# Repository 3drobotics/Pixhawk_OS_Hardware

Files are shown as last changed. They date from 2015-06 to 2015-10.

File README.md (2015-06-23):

# Pixhawk_OS_Hardware
Design files for the open hardware designs used by 3DR

Some of the files in this Repository are derivitives of the PX4 project.

PX4 is an open hardware design, following the OSHW 1.1 definition licensed under the Creative Commons Attribution-ShareAlike 3.0 Unported (CC BY-SA 3.0) license.  Website at: http://pixhawk.ethz.ch/px4/

That includes 
FMUv3
IMUv3
PSMv3

the following licence applies to these files.

UNLESS OTHERWISE MUTUALLY AGREED TO BY THE PARTIES IN WRITING, LICENSOR OFFERS THE WORK AS-IS AND MAKES NO REPRESENTATIONS OR WARRANTIES OF ANY KIND CONCERNING THE WORK, EXPRESS, IMPLIED, STATUTORY OR OTHERWISE, INCLUDING, WITHOUT LIMITATION, WARRANTIES OF TITLE, MERCHANTIBILITY, FITNESS FOR A PARTICULAR PURPOSE, NONINFRINGEMENT, OR THE ABSENCE OF LATENT OR OTHER DEFECTS, ACCURACY, OR THE PRESENCE OF ABSENCE OF ERRORS, WHETHER OR NOT DISCOVERABLE. SOME JURISDICTIONS DO NOT ALLOW THE EXCLUSION OF IMPLIED WARRANTIES, SO SUCH EXCLUSION MAY NOT APPLY TO YOU. EXCEPT TO THE EXTENT REQUIRED BY APPLICABLE LAW, IN NO EVENT WILL LICENSOR BE LIABLE TO YOU ON ANY LEGAL THEORY FOR ANY SPECIAL, INCIDENTAL, CONSEQUENTIAL, PUNITIVE OR EXEMPLARY DAMAGES ARISING OUT OF THIS LICENSE OR THE USE OF THE WORK, EVEN IF LICENSOR HAS BEEN ADVISED OF THE POSSIBILITY OF SUCH DAMAGES. http://creativecommons.org/licenses/by-sa/3.0/

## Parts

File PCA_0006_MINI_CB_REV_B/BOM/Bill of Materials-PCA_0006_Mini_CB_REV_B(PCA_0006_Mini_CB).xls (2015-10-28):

Manufacturer 1 | Manufacturer Part Number 1 | Supplier Part Number 1 | 3DR_PARTNO | Description | Designator | Value | Quantity | Footprint | Mfg Part Num (Alternate) | Mfg Name (Alternate) | Supplier Unit Price 1 | Total Cost per
Molex, LLC | 5023861570 | WM4958DKR-ND | ECM0530 | Connector, Receptacle, 15Pos, 1.25MM, R/A, SMD, Tin | 1 |  | 1 | CLICKMATE_H15 |  |  | $1.67 | $1.67
Molex, LLC | 5023860470 | WM4948CT-ND | ECM0531 | Connector, Receptacle, 4Pos, 1.25MM, R/A, SMD, Tin | 2, 3 |  | 2 | CLICKMATE_H4 |  |  | $0.78 | $1.55
Molex, LLC | 5023860670 | WM3917CT-ND | ECM0532 | 1.25 W/B SGL R/A REC ASSY 6CKT | 5, 11 |  | 2 | CLICKMATE_H6 |  |  | $0.92 | $1.84
Molex, LLC | 5023860870 | WM4951CT-ND | ECM0533 | Connector, Receptacle, 8Pos, 1.25MM, R/A, SMD, Tin | 7 |  | 1 | CLICKMATE_H8 |  |  | $1.02 | $1.02
Molex, LLC | 5024940670 | WM2283CT-ND | ECM0534 | Connector, Receptacle, 6Pos, 2.00MM, R/A, PCB, Tin | 9 |  | 1 | CLICKMATE_H6_2MM |  |  | $1.04 | $1.04
TE Connectivity / Raychem | PESD0402-140 | 650-PESD0402-140 | ECM0837 | Diode, TVS, 14VWM, 40VC, 0402, SMD | D2, D3, D101, D103, D702 |  | 5 | 0402-TVS |  |  | $0.09 | $0.45
VISHAY SEMICONDUCTOR | MSS1P4-M3/89A | 2335156 | ECM0900 | Diode, Schottky, 40V, 1A, MicroSMP, SMD | D701 |  | 1 | MICROSMP |  |  | $0.12 | $0.12
AVX Corp/Kyocera Corp | KNH16C104DA5TS | 478-6878-1-ND | ECM0719 | Capacitor, Filter, 0.1uF, 25V, 2A, 0603, SMD | L1, L3, L101, L103, L701 |  | 5 | KYOCERA-KNH16-DA |  |  | $0.09 | $0.47
 |  |  | PCB0007 | PCB, Carrier Mini, PX2, Board | PCB0007 | PCB0007 | 1 |  |  |  |  | $0.00
3DR | PCA-0007 | PCA-0007 | PCA0007 | PCA, PSM, PX4, Assembly | PSM ? |  | 1 | PSM |  |  | $17.00 | $17.00
Hirose Electric Co Ltd | DF17(1.0H)-80DP-0.5V(57) | DF17(1.0H)-80DP-0.5V(57)-ND | ECM0528 | Connector, Header, 80Pos, .5MM, DUAL, SMD, Au | U$1 |  | 1 | CON-DF17-80M |  |  | $1.50 | $1.50
 |  |  |  |  |  |  |  |  |  |  |  | $0.00
 |  |  |  |  |  |  |  |  |  |  |  | $0.00
 |  |  |  |  |  |  |  |  |  |  |  | $0.00
 |  |  |  |  |  |  |  |  |  |  |  | $0.00
 |  |  |  |  |  |  |  |  |  |  |  | $0.00
 |  |  |  |  |  |  |  |  |  |  |  | $0.00
 |  |  |  |  |  |  |  |  |  |  |  | $0.00
 |  |  |  |  |  |  |  |  |  |  |  | $0.00
 |  |  |  |  |  |  |  |  |  |  |  | $0.00
 |  |  |  |  |  |  |  |  |  |  |  | $0.00
 |  |  |  |  |  |  |  |  |  |  |  | $0.00
 |  |  |  |  |  |  |  |  |  |  |  | $0.00
 |  |  |  |  |  |  |  |  |  |  |  | $0.00
 |  |  |  |  |  |  |  |  |  |  |  | $0.00
 |  |  |  |  |  |  |  |  |  |  |  | $0.00
 |  |  |  |  |  |  |  |  |  |  |  | $0.00
 |  |  |  |  |  |  |  |  |  |  |  | $0.00
 |  |  |  |  |  |  |  |  |  |  |  | $0.00
 |  |  |  |  |  |  |  |  |  |  |  | $0.00
 |  |  |  |  |  |  |  |  |  |  |  | $0.00
 |  |  |  |  |  |  |  |  |  |  |  | $0.00
 |  |  |  |  |  |  |  |  |  |  |  | $0.00
 |  |  |  |  |  |  |  |  |  |  |  | $0.00
 |  |  |  |  |  |  |  |  |  |  |  | $0.00
 |  |  |  |  |  |  |  |  |  |  |  | $0.00
 |  |  |  |  |  |  |  |  |  |  |  | $0.00
 |  |  |  |  |  |  |  |  |  |  |  | $0.00
 |  |  |  |  |  |  |  |  |  |  |  | $0.00
 |  |  |  |  |  |  |  |  |  |  |  | $0.00
 |  |  |  |  |  |  |  |  |  |  |  | $0.00
 |  |  |  |  |  |  |  |  |  |  |  | $0.00
 |  |  |  |  |  | Total Qty. | 21 |  |  |  | Total Cost | $26.67

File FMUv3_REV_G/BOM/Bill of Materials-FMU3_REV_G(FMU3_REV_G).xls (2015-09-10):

Manufacturer 1 | Manufacturer Part Number 1 | Supplier Part Number 1 | 3DR_PARTNO | Description | Designator | Value | Quantity | Footprint | Mfg Part Num (Alternate) | Mfg Name (Alternate) | Supplier Unit Price 1 | Total Cost per
Yageo | CC0402ZRY5V7BB104 | 311-1047-1-ND | ECM0700 | CAP CER 0.1UF 16V Y5V 0402 | C1001, C3001, C3002, C3003, C3004, C4003, C4005, C4006, C5001, C5005, C5007, C5009, C5010, C5011, C5012, C5014, C5015, C7001, C7002, C7003, C7006, C8001, C8002, C8003, C10002 | 0u1 | 25 | 0402-CAP |  |  | $0.00242 | $0.06
TDK Corporation | C1005C0G1H080C050BA | 445-4890-1-ND | ECM0710 | CAP CER 8PF 50V C0G 0402 | C1002, C1003, C7004, C7005 | 8p | 4 | 0402-CAP |  |  | $0.01 | $0.02
TDK Corporation | C1608X6S1C225K080AC | 445-7438-1-ND | ECM0619 | CAP CER 2.2UF 16V 10% X6S 0603 | C4001, C4002, C5013, C5016 | 2u2 | 4 | 0603-CAP |  |  | $0.06 | $0.22
TDK Corporation | C1005X6S1E224K050BC | 445-7362-1-ND | ECM | CAP CER 0.22UF 25V 10% X7R 0402 | C4007 | 0u22 | 1 | 0402-CAP |  |  | $0.02 | $0.02
Samsung Electro-Mechanics America, Inc. | CL21B475KOFNNNE | 1276-2873-1-ND | ECM0622 | CAP CER 4.7UF 16V 10% X7R 0805 | C4008 | 4u7 | 1 | 0805 |  |  | $0.06 | $0.06
Samsung Electro-Mechanics America, Inc. | CL21A106KAYNNNE | 1276-2891-1-ND | ECM0714 | CAP CER 10UF 25V 10% X5R 0805 | C5002, C10001 | 10u/25 | 2 | 0805-CAP |  |  | $0.06 | $0.11
Yageo | CC0402KRX7R7BB103 | 311-1042-1-ND | ECM0711 | CAP CER 10000PF 16V 10% X7R 0402 | C5003, C10003 | 10n | 2 | 0402-CAP |  |  | $0.00249 | $0.00498
Yageo | CC0603ZRY5V7BB105 | 311-1372-1-ND | ECM0705 | CAP CER 1UF 16V Y5V 0603 | C5004, C10005 | 1u | 2 | 0603-CAP |  |  | $0.01 | $0.02
Samsung Electro-Mechanics America, Inc. | CL21A226MAQNNNE | 1276-2908-1-ND | ECM0715 | CAP CER 22UF 25V 20% X5R 0805 | C5006, C5008 | 22u/25V | 2 | 0805-CAP |  |  | $0.39 | $0.78
Murata Electronics North America | GRM21BR60G107ME15L | 490-10510-1-ND |  |  | C5100, C5101 | 100uF | 2 | C0805 |  |  | $0.43 | $0.86
TDK Corporation | C1608X5R1A106K080AC | 445-7486-1-ND | ECM0712 | CAP CER 10UF 10V 10% X5R 0603 | C10004 | 10u | 1 | 0603-CAP |  |  | $0.13 | $0.13
ON Semiconductor | RB751V40T1G | RB751V40T1GOSCT-ND | ECM0839 | DIODE SCHOTTKY 30V 0.03A SOD323 | D5001 | 30V | 1 | SOD323 |  |  | $0.05 | $0.05
TE Connectivity / Raychem | PESD0402-140 | 650-PESD0402-140 | ECM0837 | TVS DIODE 14VWM 40VC 0402 | D8001, D8002 | 40v | 2 | 0402-TVS |  |  | $0.09 | $0.19
NXP Semiconductors | PMEG2005CT,215 | 568-6500-1-ND | ECM0838 | DIODE SCHOTTKY 20V 500MA TO236AB | D10001 | 20V | 1 | SOT23-3 |  |  | $0.10 | $0.10
Bel Fuse Inc. | 0ZCA0035FF2G | 507-1479-1-ND | ECM0802 | PTC RESTTBLE 0.35A 16V CHIP 1206 | F10001 | 0.35A | 1 | PTC-1206 |  |  | $0.11 | $0.11
Molex Inc. | 0473460001 | WM17141DKR-ND | ECM0486 | MICRO USB B, BOTTOM MOUNT | J2001 |  | 1 | MOLEX-47346-0001 |  |  | $0.52 | $0.52
 |  |  |  |  | JP1 |  | 1 | SJ_3_NO_PLACE_1-2_short |  |  |  | $0.00
AVX Corp/Kyocera Corp | KNH16C104DA5TS | 478-6878-1-ND | ECM0719 | FILTER CAP 0.1UF 2A 25V 0603 | L2001, L2002, L5001 | 0u1 | 3 | KYOCERA-KNH16-DA |  |  | $0.09 | $0.26
Kingbright | APTD1608CGCK | 754-1545-2-ND | ECM0494 | LED GREEN ROUND CLEAR SMD | LED1, LED2, LED6001, LED6002, LED6003, LED6004, LED6005, LED6006, LED6007, LED6008, LED6009 | GREEN | 11 | 0603-LED-Blue |  |  | $0.07 | $0.78
Kingbright | APTD1608SECK/J4-PF | 754-1802-1-ND | ECM0515 | LED 1.6X0.8 DOME ORN CLEAR SMD | LED6010, LED6011 | AMBER | 2 | 0603-LED |  |  | $0.18 | $0.37
 |  |  | PCB005 | PCB,FMU, PX2, Board | PCB005 | PCB005 | 1 |  |  |  |  | $0.00
Infineon Technologies | MMBT 3906 LT1 | MMBT3906LT1INCT-ND | ECM0833 | TRANSISTOR SWITCHING PNP SOT-23 | Q5001 |  | 1 | SOT23-BEC |  |  | $0.03 | $0.03
Diodes Incorporated | BSS123-7-F | BSS123-FDICT-ND | ECM0547 | MOSFET N-CH 100V 170MA SOT23-3 | Q6001 | 100V | 1 | SOT23 |  |  | $0.06 | $0.06
Yageo | RC0402FR-07220RL | 311-220LRCT-ND | ECM0821 | RES 220 OHM 1/16W 1% 0402 SMD | R1, R2, R1022, R4001, R4002, R6003, R6004, R6005, R6006, R6007, R6008, R6009, R6010, R6011, R6012, R6013, R6014, R6015, R7003, R7004, R7010, R7011, R7012 | 220R | 23 | 0402-RES |  |  | $0.00176 | $0.04
Yageo | RC0402FR-07470RL | 311-470LRCT-ND | ECM0823 | RES 470 OHM 1/16W 1% 0402 SMD | R1001 | 470R | 1 | 0402-RES |  |  | $0.00176 | $0.00176
Yageo | RC0402FR-0710KL | 311-10.0KLRCT-ND | ECM0800 | RES 10K OHM 1/16W 1% 0402 SMD | R1002, R5001, R5006, R6002, R7001, R7002, R8001 | 10K | 7 | 0402-RES |  |  | $0.00176 | $0.01
Panasonic Electronic Components | ERA-2AEB103X | P10KDCCT-ND | ECM0810 | RES 10K OHM 1/16W .1% 0402 SMD | R2001, R2002 | 10K | 2 | 0402-RES |  |  | $0.07 | $0.15
Yageo | RC0402FR-071ML | 311-1.00MLRCT-ND | ECM0806 | RES 1M OHM 1/16W 1% 0402 SMD | R2003, R2004 | 1M | 2 | 0402-RES |  |  | $0.00176 | $0.00352
Yageo | RC0402FR-071K5L | 311-1.50KLRCT-ND | ECM0803 | RES 1.5K OHM 1/16W 1% 0402 SMD | R3001, R3002, R3003, R3004, R6017 | 1K5 | 5 | 0402-RES |  |  | $0.00176 | $0.01
Yageo | RC0402FR-07120RL | 311-120LRCT-ND | ECM0820 | RES 120 OHM 1/16W 1% 0402 SMD | R3005, R3006, R3007, R3008, R3009, R3010 | 120R | 6 | 0402-RES |  |  | $0.00176 | $0.01
Samsung Electro-Mechanics America, Inc. | RC1005F182CS | 1276-4039-1-ND | ECM0807 | RES 1.8K OHM 1/16W 1% 0402 | R5002 | 1K8 | 1 | 0402-RES |  |  | $0.002 | $0.002
Samsung Electro-Mechanics America, Inc. | RC1608J100CS | 1276-5014-1-ND | ECM0811 | RES 10 OHM 1/10W 5% 0603 | R5003 | 10R | 1 | 0603-RES |  |  | $0.00164 | $0.00164
Samsung Electro-Mechanics America, Inc. | RC1005F102CS | 1276-3430-1-ND | ECM0804 | RES 1K OHM 1/16W 1% 0402 | R5005, R6001 | 1K | 2 | 0402-RES |  |  | $0.002 | $0.004
Panasonic | ERJ-2GEJ680X | 667-ERJ-2GEJ680X | ECM0816 | Thick Film Resistors - SMD 0402 68ohms 5% Tol | R6016 | 68R | 1 | 0402-RES |  |  | $0.00208 | $0.00208
Yageo | RC0402FR-07100KL | 311-100KLRCT-ND | ECM0818 | RES 100K OHM 1/16W 1% 0402 SMD | R10001 | 100K | 1 | 0402-RES |  |  | $0.00176 | $0.00176
Panasonic Electronic Components | EXB-2HV104JV | Y1104CT-ND | ECM0101 | RES ARRAY 100K OHM 8 RES 1506 | RN2001 | 100K | 1 | EXB2HV |  |  | $0.06 | $0.06
Panasonic Electronic Components | EXB-2HV103JV | Y1103CT-ND | ECM0546 | RES ARRAY 10K OHM 8 RES 1506 | RN2002 | 10K | 1 | EXB2HV |  |  | $0.06 | $0.06
Panasonic Electronic Components | EXB-2HV121JV | Y1121CT-ND | EMC, EMC, ECM0266, ECM0266 | RES ARRAY 120 OHM 8 RES 1506 | RN3001, RN3002, RN8001, RN8002 | 120R | 4 | EXB2HV |  |  | $0.06 | $0.26
InvenSense | MPU-9250 | 1428-1019-2-ND |  |  | U405 |  | 1 | MPU-9250 |  |  | $5.11 | $5.11
STMicroelectronics | STM32F427VIT6 |  |  | REV 3 Silicon or later IC MCU ARM 2MB FLASH 100LQFP | U1001 |  | 1 | TQFP100 |  |  | $9.75 | $9.75
Cypress Semiconductor Corp | FM25V02A-G | 428-3386-ND |  | IC FRAM 256KBIT 40MHZ 8SOIC | U1002 | 256Kb | 1 | SO08 |  |  | $3.31 | $3.31
ON Semiconductor | NUF2042XV6T1G | NUF2042XV6T1GOSDKR-ND | ECM0836 | IC FILTER USB ESD PROTECT SOT363 | U2001 |  | 1 | SOT563-6 |  |  | $0.15 | $0.15
3M | 2908-05WB-MG | 3M5607CT-ND | ECM0485 | CONN MICRO SD CARD PUSH-PUSH R/A | U2002 |  | 1 | MICROSD |  |  | $1.98 | $1.98
Texas Instruments | TXS0108ERGYR | 296-24806-1-ND | ECM0845 | IC XLATR VOLT-LVL 8B BDIR 20QFN | U3001, U3002, U8001 |  | 3 | QFN20-RGY |  |  | $0.85 | $2.56
Maxim Integrated | MAX3051EKA+T | MAX3051EKA+TCT-ND | ECM0831 | IC TXRX CAN 1MBPS SOT23-8 | U3003, U3004 | CAN | 2 | SOT23-8 |  |  | $1.93 | $3.86
Honeywell Microelectronics & Precision Sensors | HMC5983-TR | 342-1092-1-ND | ECM0672 | IC COMPASS 3 AXIS 16-LCC | U4002 |  | 1 | HMC5983-new |  |  | $1.50 | $1.50
Measurement Specialties | MS561101BA03-50 | 824-MS561101BA03-50 | ECM0835 | Board Mount Pressure Sensors | U4003 | 10-1200mbar | 1 | MS5611-01BA |  |  | $6.67 | $6.67
Micrel Inc. | MIC5332-SSYMT TR | 576-4110-1-ND | ECM0832 | IC REG LDO 3.3V 0.3A 8TMLF | U5001, U10002 | 3.3V | 2 | MLF-8-EPAD |  |  | $0.80 | $1.61
STMicroelectronics | STM32F100C8T6B | 497-10499-ND | EMC0842 | MCU 32BIT ARM 64K FLASH 48LQFP | U7001 |  | 1 | TQFP48 |  |  | $1.59 | $1.59
Texas Instruments | SN74LVC8T245RHLR | 296-18595-2-ND |  |  | U8002 |  | 1 | QFN20-RGY |  |  | $0.49 | $0.49
NXP Semiconductors | 74LVC2G240DP,125 | 568-8979-1-ND | ECM0817 | IC INVERTER DUAL 4-INPUT 8TSSOP | U8003 | INV | 1 | TSSOP8_SOT505-2 |  |  | $0.14 | $0.14
Texas Instruments | BQ24313DSGT | 296-23933-1-ND | ECM0824 | IC LI+ CHARGER FRONT END 8-SON | U10001 |  | 1 | QFN8-DSG |  |  | $0.87 | $0.87
Hirose Electric Co Ltd | DF40C(2.0)-20DS-0.4V(51) | H11905CT-ND | ECM0517 | CONN RCPT 20POS 0.4MM SMD GOLD | U$2 |  | 1 | DF-40C-20DS |  |  | $0.42 | $0.42
Hirose Electric Co Ltd | DF17(3.0H)-80DS-0.5V(57) | DF17(3.0H)-80DS-0.5V(57)-ND | ECM0518 | CONN RECEPT 80POS .5MM SMD W/FIT | U$9001 |  | 1 | CON-DF17-80F |  |  | $1.34 | $1.34
NDK | NX3225SA-24.000MHZ-STD-CSR-1 | 644-1052-1-ND | ECM0708 | CRYSTAL 24MHZ 8PF SMD | X1001, X7001 | 24MHz | 2 | OSCILLATOR-3.2X2.5 |  |  | $0.39 | $0.79
 |  |  |  |  |  |  |  |  |  |  |  | $0.00
 |  |  |  |  |  |  |  |  |  |  |  | $0.00
 |  |  |  |  |  |  |  |  |  |  |  | $0.00
 |  |  |  |  |  |  |  |  |  |  |  | $0.00
 |  |  |  |  |  |  |  |  |  |  |  | $0.00
 |  |  |  |  |  |  |  |  |  |  |  | $0.00
 |  |  |  |  |  |  |  |  |  |  |  | $0.00
 |  |  |  |  |  |  |  |  |  |  |  | $0.00
 |  |  |  |  |  |  |  |  |  |  |  | $0.00
 |  |  |  |  |  |  |  |  |  |  |  | $0.00
 |  |  |  |  |  |  |  |  |  |  |  | $0.00
 |  |  |  |  |  |  |  |  |  |  |  | $0.00
 |  |  |  |  |  |  |  |  |  |  |  | $0.00
 |  |  |  |  |  |  |  |  |  |  |  | $0.00
 |  |  |  |  |  |  |  |  |  |  |  | $0.00
 |  |  |  |  |  |  |  |  |  |  |  | $0.00
 |  |  |  |  |  |  |  |  |  |  |  | $0.00
 |  |  |  |  |  |  |  |  |  |  |  | $0.00
 |  |  |  |  |  |  |  |  |  |  |  | $0.00
 |  |  |  |  |  |  |  |  |  |  |  | $0.00
 |  |  |  |  |  |  |  |  |  |  |  | $0.00
 |  |  |  |  |  |  |  |  |  |  |  | $0.00
 |  |  |  |  |  |  |  |  |  |  |  | $0.00
 |  |  |  |  |  |  |  |  |  |  |  | $0.00
 |  |  |  |  |  |  |  |  |  |  |  | $0.00
 |  |  |  |  |  |  |  |  |  |  |  | $0.00
 |  |  |  |  |  |  |  |  |  |  |  | $0.00
 |  |  |  |  |  |  |  |  |  |  |  | $0.00
 |  |  |  |  |  |  |  |  |  |  |  | $0.00
 |  |  |  |  |  |  |  |  |  |  |  | $0.00
 |  |  |  |  |  |  |  |  |  |  |  | $0.00
 |  |  |  |  |  | Total Qty. | 152 |  |  |  | Total Cost | $47.52
 |  |  |  |  |  | APPROVALS
PART NUMBER (3DR ERP) | BOM REVISION | REV. DATE |  | REF. DRAWING/SCHEMATIC: |  | Dept. | Name | Signature | Date
FMU3_REV_G |  | 9/09/2015 |  | FMU3_REV_G.PrjPcb |  | Design Engineering (PR)
PRODUCT DESCRIPTION | ECR/ECO/ECN |  |  |  |  | Dir. Of Eng. | Tim M.
FMU3_REV_G.PrjPcb |  | Parts Info: |  | N/A |  | Operations Mgmt | Lorenzo L.
Total parts = | 152 | Unique Parts: |  | N/A |  | Production | Juan V.
Feeder requirement: | N/A | Total Placements: 0 |  | N/A

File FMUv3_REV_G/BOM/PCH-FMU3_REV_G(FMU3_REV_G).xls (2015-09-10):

 | FMU PCBA BOM
 |  |  |  |  |  |  |  |  |  |  |  | BOM template_Rev.01
PCBA BOM Release Date: |  |  |  | PCBA Function: |  | PCBA No.: |  | Manufacturing Location: | BOM Release Purpose:
 | PCBA BOM Rev.: |  |  | Product Description: | FMU3_REV_G | Product No.: |  | Jabil
 | Released By: |  |  | Project No.: Solo |  | ECN No.:
BOM Change History for BOM update:
Item No. | PCH Part No. | Designator | Quantity | MPN | Manufacturer | Footprint | General Description |  | Value | Action (A/M/D) | ECN No. | Remark
Full BOM for new BOM creation, for BOM update, just fill in the changed item(s) in above columns.
Item No. | PCH Part No. | Designator | Quantity | Manufacturer Part Number 1 | Manufacturer 1 | Footprint | Description |  | Value | Action (A/M/D) | ECN No. | Remark
 |  | C1001, C3001, C3002, C3003, C3004, C4003, C4005, C4006, C5001, C5005, C5007, C5009, C5010, C5011, C5012, C5014, C5015, C7001, C7002, C7003, C7006, C8001, C8002, C8003, C10002 | 25 | CC0402ZRY5V7BB104 | Yageo | 0402-CAP | CAP CER 0.1UF 16V Y5V 0402 |  | 0u1
 |  | C1002, C1003, C7004, C7005 | 4 | C1005C0G1H080C050BA | TDK Corporation | 0402-CAP | CAP CER 8PF 50V C0G 0402 |  | 8p
 |  | C4001, C4002, C5013, C5016 | 4 | C1608X6S1C225K080AC | TDK Corporation | 0603-CAP | CAP CER 2.2UF 16V 10% X6S 0603 |  | 2u2
 |  | C4007 | 1 | C1005X6S1E224K050BC | TDK Corporation | 0402-CAP | CAP CER 0.22UF 25V 10% X7R 0402 |  | 0u22
 |  | C4008 | 1 | CL21B475KOFNNNE | Samsung Electro-Mechanics America, Inc. | 0805 | CAP CER 4.7UF 16V 10% X7R 0805 |  | 4u7
 |  | C5002, C10001 | 2 | CL21A106KAYNNNE | Samsung Electro-Mechanics America, Inc. | 0805-CAP | CAP CER 10UF 25V 10% X5R 0805 |  | 10u/25
 |  | C5003, C10003 | 2 | CC0402KRX7R7BB103 | Yageo | 0402-CAP | CAP CER 10000PF 16V 10% X7R 0402 |  | 10n
 |  | C5004, C10005 | 2 | CC0603ZRY5V7BB105 | Yageo | 0603-CAP | CAP CER 1UF 16V Y5V 0603 |  | 1u
 |  | C5006, C5008 | 2 | CL21A226MAQNNNE | Samsung Electro-Mechanics America, Inc. | 0805-CAP | CAP CER 22UF 25V 20% X5R 0805 |  | 22u/25V
 |  | C5100, C5101 | 2 | GRM21BR60G107ME15L | Murata Electronics North America | C0805 |  |  | 100uF
 |  | C10004 | 1 | C1608X5R1A106K080AC | TDK Corporation | 0603-CAP | CAP CER 10UF 10V 10% X5R 0603 |  | 10u
 |  | D5001 | 1 | RB751V40T1G | ON Semiconductor | SOD323 | DIODE SCHOTTKY 30V 0.03A SOD323 |  | 30V
 |  | D8001, D8002 | 2 | PESD0402-140 | TE Connectivity / Raychem | 0402-TVS | TVS DIODE 14VWM 40VC 0402 |  | 40v
 |  | D10001 | 1 | PMEG2005CT,215 | NXP Semiconductors | SOT23-3 | DIODE SCHOTTKY 20V 500MA TO236AB |  | 20V
 |  | F10001 | 1 | 0ZCA0035FF2G | Bel Fuse Inc. | PTC-1206 | PTC RESTTBLE 0.35A 16V CHIP 1206 |  | 0.35A
 |  | J2001 | 1 | 0473460001 | Molex Inc. | MOLEX-47346-0001 | MICRO USB B, BOTTOM MOUNT
 |  | JP1 | 1 |  |  | SJ_3_NO_PLACE_1-2_short
 |  | L2001, L2002, L5001 | 3 | KNH16C104DA5TS | AVX Corp/Kyocera Corp | KYOCERA-KNH16-DA | FILTER CAP 0.1UF 2A 25V 0603 |  | 0u1
 |  | LED1, LED2, LED6001, LED6002, LED6003, LED6004, LED6005, LED6006, LED6007, LED6008, LED6009 | 11 | APTD1608CGCK | Kingbright | 0603-LED-Blue | LED GREEN ROUND CLEAR SMD |  | GREEN
 |  | LED6010, LED6011 | 2 | APTD1608SECK/J4-PF | Kingbright | 0603-LED | LED 1.6X0.8 DOME ORN CLEAR SMD |  | AMBER
 |  | PCB005 | 1 |  |  |  | PCB,FMU, PX2, Board |  | PCB005
 |  | Q5001 | 1 | MMBT 3906 LT1 | Infineon Technologies | SOT23-BEC | TRANSISTOR SWITCHING PNP SOT-23
 |  | Q6001 | 1 | BSS123-7-F | Diodes Incorporated | SOT23 | MOSFET N-CH 100V 170MA SOT23-3 |  | 100V
 |  | R1, R2, R1022, R4001, R4002, R6003, R6004, R6005, R6006, R6007, R6008, R6009, R6010, R6011, R6012, R6013, R6014, R6015, R7003, R7004, R7010, R7011, R7012 | 23 | RC0402FR-07220RL | Yageo | 0402-RES | RES 220 OHM 1/16W 1% 0402 SMD |  | 220R
 |  | R1001 | 1 | RC0402FR-07470RL | Yageo | 0402-RES | RES 470 OHM 1/16W 1% 0402 SMD |  | 470R
 |  | R1002, R5001, R5006, R6002, R7001, R7002, R8001 | 7 | RC0402FR-0710KL | Yageo | 0402-RES | RES 10K OHM 1/16W 1% 0402 SMD |  | 10K
 |  | R2001, R2002 | 2 | ERA-2AEB103X | Panasonic Electronic Components | 0402-RES | RES 10K OHM 1/16W .1% 0402 SMD |  | 10K
 |  | R2003, R2004 | 2 | RC0402FR-071ML | Yageo | 0402-RES | RES 1M OHM 1/16W 1% 0402 SMD |  | 1M
 |  | R3001, R3002, R3003, R3004, R6017 | 5 | RC0402FR-071K5L | Yageo | 0402-RES | RES 1.5K OHM 1/16W 1% 0402 SMD |  | 1K5
 |  | R3005, R3006, R3007, R3008, R3009, R3010 | 6 | RC0402FR-07120RL | Yageo | 0402-RES | RES 120 OHM 1/16W 1% 0402 SMD |  | 120R
 |  | R5002 | 1 | RC1005F182CS | Samsung Electro-Mechanics America, Inc. | 0402-RES | RES 1.8K OHM 1/16W 1% 0402 |  | 1K8
 |  | R5003 | 1 | RC1608J100CS | Samsung Electro-Mechanics America, Inc. | 0603-RES | RES 10 OHM 1/10W 5% 0603 |  | 10R
 |  | R5005, R6001 | 2 | RC1005F102CS | Samsung Electro-Mechanics America, Inc. | 0402-RES | RES 1K OHM 1/16W 1% 0402 |  | 1K
 |  | R6016 | 1 | ERJ-2GEJ680X | Panasonic | 0402-RES | Thick Film Resistors - SMD 0402 68ohms 5% Tol |  | 68R
 |  | R10001 | 1 | RC0402FR-07100KL | Yageo | 0402-RES | RES 100K OHM 1/16W 1% 0402 SMD |  | 100K
 |  | RN2001 | 1 | EXB-2HV104JV | Panasonic Electronic Components | EXB2HV | RES ARRAY 100K OHM 8 RES 1506 |  | 100K
 |  | RN2002 | 1 | EXB-2HV103JV | Panasonic Electronic Components | EXB2HV | RES ARRAY 10K OHM 8 RES 1506 |  | 10K
 |  | RN3001, RN3002, RN8001, RN8002 | 4 | EXB-2HV121JV | Panasonic Electronic Components | EXB2HV | RES ARRAY 120 OHM 8 RES 1506 |  | 120R
 |  | U405 | 1 | MPU-9250 | InvenSense | MPU-9250
 |  | U1001 | 1 | STM32F427VIT6 | STMicroelectronics | TQFP100 | REV 3 Silicon or later IC MCU ARM 2MB FLASH 100LQFP
 |  | U1002 | 1 | FM25V02A-G | Cypress Semiconductor Corp | SO08 | IC FRAM 256KBIT 40MHZ 8SOIC |  | 256Kb
 |  | U2001 | 1 | NUF2042XV6T1G | ON Semiconductor | SOT563-6 | IC FILTER USB ESD PROTECT SOT363
 |  | U2002 | 1 | 2908-05WB-MG | 3M | MICROSD | CONN MICRO SD CARD PUSH-PUSH R/A
 |  | U3001, U3002, U8001 | 3 | TXS0108ERGYR | Texas Instruments | QFN20-RGY | IC XLATR VOLT-LVL 8B BDIR 20QFN
 |  | U3003, U3004 | 2 | MAX3051EKA+T | Maxim Integrated | SOT23-8 | IC TXRX CAN 1MBPS SOT23-8 |  | CAN
 |  | U4002 | 1 | HMC5983-TR | Honeywell Microelectronics & Precision Sensors | HMC5983-new | IC COMPASS 3 AXIS 16-LCC
 |  | U4003 | 1 | MS561101BA03-50 | Measurement Specialties | MS5611-01BA | Board Mount Pressure Sensors |  | 10-1200mbar
 |  | U5001, U10002 | 2 | MIC5332-SSYMT TR | Micrel Inc. | MLF-8-EPAD | IC REG LDO 3.3V 0.3A 8TMLF |  | 3.3V
 |  | U7001 | 1 | STM32F100C8T6B | STMicroelectronics | TQFP48 | MCU 32BIT ARM 64K FLASH 48LQFP
 |  | U8002 | 1 | SN74LVC8T245RHLR | Texas Instruments | QFN20-RGY
 |  | U8003 | 1 | 74LVC2G240DP,125 | NXP Semiconductors | TSSOP8_SOT505-2 | IC INVERTER DUAL 4-INPUT 8TSSOP |  | INV
 |  | U10001 | 1 | BQ24313DSGT | Texas Instruments | QFN8-DSG | IC LI+ CHARGER FRONT END 8-SON
 |  | U$2 | 1 | DF40C(2.0)-20DS-0.4V(51) | Hirose Electric Co Ltd | DF-40C-20DS | CONN RCPT 20POS 0.4MM SMD GOLD
 |  | U$9001 | 1 | DF17(3.0H)-80DS-0.5V(57) | Hirose Electric Co Ltd | CON-DF17-80F | CONN RECEPT 80POS .5MM SMD W/FIT
 |  | X1001, X7001 | 2 | NX3225SA-24.000MHZ-STD-CSR-1 | NDK | OSCILLATOR-3.2X2.5 | CRYSTAL 24MHZ 8PF SMD |  | 24MHz
Remark:
This form is used for both first Engineering BOM entry request and BOM change update request, if it is for BOM change, engineer needs to fill in the 'Change History' column as well as update the 'Full BOM' column .
ECN No. will be provided by PCH, date code should be included, e.g. release on 30 Oct.,2014, the ECN No. is ECN20141030xxxx
Action: A-Add Part; D-Delete Part; M-Modify part property e.g description, qty, material etc.

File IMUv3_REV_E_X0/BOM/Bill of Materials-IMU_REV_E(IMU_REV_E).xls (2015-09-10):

Manufacturer 1 | Manufacturer Part Number 1 | Supplier Part Number 1 | 3DR_PARTNO | Description | Designator | Value | Quantity | Footprint | Mfg Part Num (Alternate) | Mfg Name (Alternate) | Supplier Unit Price 1 | Total Cost per
Yageo | CC0805ZKY5V6BB106 | 311-1355-1-ND | ECM0713 | Capacitor, 10uF, 10V, Y5V, 0805, Ceramic | C1, C4, C6, C13 | 10u | 4 | 0805-CAP |  |  | $0.03 | $0.12
Yageo | CC0402ZRY5V7BB104 | 311-1047-1-ND | ECM0700 | Capacitor, 0.1uF, 16V, Y5V, 0402, Ceramic | C2, C5, C10, C12, C14 | 0u1 | 5 | 0402-CAP |  |  | $0.00242 | $0.01
Yageo | CC0402KRX7R7BB103 | 311-1042-1-ND | ECM0711 | Capacitor, 10000pF, 16V, 10%, X7R, 0402, Ceramic | C3 | 10000pF | 1 | 0402-CAP |  |  | $0.00249 | $0.00249
TDK Corporation | C1005X5R1C474K050BC | 445-4976-1-ND | ECM0704 | Capacitor, 0.47uF, 16V, 10%, X5R, 0402, Ceramic | C7 | 0u47 | 1 | 0402-CAP |  |  | $0.02 | $0.02
TDK Corporation | C1608X6S1C225K080AC | 445-7438-1-ND | ECM0619 | Capacitor, 2.2uF, 16V, 10%, X6S, 0603, Ceramic | C8, C9 | 2u2 | 2 | 0603-CAP |  |  | $0.06 | $0.11
PennEngineering | PEM-SMTSO-M1.6-2-ET | PEM-SMTSO-M1.6-2-ET | PRT0438 | Fastener, M1.6x2mm, SMTSO, Carbon Steel | Nut 1, Nut 2, Nut 3, Nut 4 |  | 4 | PEM-SMTSO-M1.6-2-ET |  |  | $0.70 | $2.80
Hirose Electric Co Ltd | DF40C-20DP-0.4V(51) | H11618CT-ND | ECM0510 | Connector, HDR, 20Pos, 0.4mm, SMD, GOLD | P1 | DF40C-20DP-0.4V(51) | 1 | DF40C-20-DP |  |  | $0.34 | $0.34
 |  |  | PCB0004 | IMU PCB | PCB0004 | PCB0004 | 1 |  |  |  |  | $0.00
Rohm Semiconductor | ESR03EZPJ5R1 | RHM5.1DTR-ND |  | RES SMD 5.1 OHM 5% 1/4W 0603 | R2, R3, R4, R5 | 5R5, 5R5, 5R5, 2.2R | 4 | R0603 |  |  | $0.01 | $0.03
STMICROELECTRONICS | L3GD20 | 73T0644 | ECM0827 | Sensor, Low-power, Three-axis, Angular rate | U1 |  | 1 | L3GD20 |  |  | $3.22 | $3.22
STMicroelectronics | LSM303DTR | 497-13819-1-ND | ECM0828 | Module, 3D Accelerometer, 3D Magnetometer | U2 |  | 1 | LSM303D |  |  | $1.50 | $1.50
InvenSense | MPU-9250 | 1428-1019-2-ND |  |  | U3_A |  | 1 | MPU-9250 |  |  | $5.11 | $5.11
Measurement Specialties | MS561101BA03-50 | 824-MS561101BA03-50 | ECM0835 | Board, Digital pressure sensor I2C/SPI | U4 |  | 1 | MS5611-01BA |  |  | $6.67 | $6.67
 |  |  |  |  |  |  |  |  |  |  |  | $0.00
 |  |  |  |  |  |  |  |  |  |  |  | $0.00
 |  |  |  |  |  |  |  |  |  |  |  | $0.00
 |  |  |  |  |  |  |  |  |  |  |  | $0.00
 |  |  |  |  |  |  |  |  |  |  |  | $0.00
 |  |  |  |  |  |  |  |  |  |  |  | $0.00
 |  |  |  |  |  |  |  |  |  |  |  | $0.00
 |  |  |  |  |  |  |  |  |  |  |  | $0.00
 |  |  |  |  |  |  |  |  |  |  |  | $0.00
 |  |  |  |  |  |  |  |  |  |  |  | $0.00
 |  |  |  |  |  |  |  |  |  |  |  | $0.00
 |  |  |  |  |  |  |  |  |  |  |  | $0.00
 |  |  |  |  |  |  |  |  |  |  |  | $0.00
 |  |  |  |  |  |  |  |  |  |  |  | $0.00
 |  |  |  |  |  |  |  |  |  |  |  | $0.00
 |  |  |  |  |  |  |  |  |  |  |  | $0.00
 |  |  |  |  |  |  |  |  |  |  |  | $0.00
 |  |  |  |  |  |  |  |  |  |  |  | $0.00
 |  |  |  |  |  |  |  |  |  |  |  | $0.00
 |  |  |  |  |  |  |  |  |  |  |  | $0.00
 |  |  |  |  |  |  |  |  |  |  |  | $0.00
 |  |  |  |  |  |  |  |  |  |  |  | $0.00
 |  |  |  |  |  |  |  |  |  |  |  | $0.00
 |  |  |  |  |  |  |  |  |  |  |  | $0.00
 |  |  |  |  |  |  |  |  |  |  |  | $0.00
 |  |  |  |  |  |  |  |  |  |  |  | $0.00
 |  |  |  |  |  |  |  |  |  |  |  | $0.00
 |  |  |  |  |  |  |  |  |  |  |  | $0.00
 |  |  |  |  |  |  |  |  |  |  |  | $0.00
 |  |  |  |  |  |  |  |  |  |  |  | $0.00
 |  |  |  |  |  |  |  |  |  |  |  | $0.00
 |  |  |  |  |  | Total Qty. | 27 |  |  |  | Total Cost | $19.94
 |  |  |  |  |  | APPROVALS
PART NUMBER (3DR ERP) | BOM REVISION | REV. DATE |  | REF. DRAWING/SCHEMATIC: |  | Dept. | Name | Signature | Date
IMU_REV_E |  | 9/09/2015 |  | IMU_REV_E.PrjPcb |  | Design Engineering (PR)
PRODUCT DESCRIPTION | ECR/ECO/ECN |  |  |  |  | Dir. Of Eng. | Tim M.
IMU_REV_E.PrjPcb |  | Parts Info: |  | N/A |  | Operations Mgmt | Lorenzo L.
Total parts = | 27 | Unique Parts: |  | N/A |  | Production | Juan V.
Feeder requirement: | N/A | Total Placements: 0 |  | N/A

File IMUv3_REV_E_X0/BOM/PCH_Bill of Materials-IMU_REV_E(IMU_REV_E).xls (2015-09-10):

 | FMU PCBA BOM
 |  |  |  |  |  |  |  |  |  |  |  | BOM template_Rev.01
PCBA BOM Release Date: |  |  |  | PCBA Function: |  | PCBA No.: |  | Manufacturing Location: | BOM Release Purpose:
 | PCBA BOM Rev.: |  |  | Product Description: | IMU_REV_E | Product No.: |  | Jabil
 | Released By: |  |  | Project No.: Solo |  | ECN No.:
BOM Change History for BOM update:
Item No. | PCH Part No. | Designator | Quantity | MPN | Manufacturer | Footprint | General Description |  | Value | Action (A/M/D) | ECN No. | Remark
Full BOM for new BOM creation, for BOM update, just fill in the changed item(s) in above columns.
Item No. | PCH Part No. | Designator | Quantity | Manufacturer Part Number 1 | Manufacturer 1 | Footprint | Description |  | Value | Action (A/M/D) | ECN No. | Remark
 |  | C1, C4, C6, C13 | 4 | CC0805ZKY5V6BB106 | Yageo | 0805-CAP | Capacitor, 10uF, 10V, Y5V, 0805, Ceramic |  | 10u
 |  | C2, C5, C10, C12, C14 | 5 | CC0402ZRY5V7BB104 | Yageo | 0402-CAP | Capacitor, 0.1uF, 16V, Y5V, 0402, Ceramic |  | 0u1
 |  | C3 | 1 | CC0402KRX7R7BB103 | Yageo | 0402-CAP | Capacitor, 10000pF, 16V, 10%, X7R, 0402, Ceramic |  | 10000pF
 |  | C7 | 1 | C1005X5R1C474K050BC | TDK Corporation | 0402-CAP | Capacitor, 0.47uF, 16V, 10%, X5R, 0402, Ceramic |  | 0u47
 |  | C8, C9 | 2 | C1608X6S1C225K080AC | TDK Corporation | 0603-CAP | Capacitor, 2.2uF, 16V, 10%, X6S, 0603, Ceramic |  | 2u2
 |  | Nut 1, Nut 2, Nut 3, Nut 4 | 4 | PEM-SMTSO-M1.6-2-ET | PennEngineering | PEM-SMTSO-M1.6-2-ET | Fastener, M1.6x2mm, SMTSO, Carbon Steel
 |  | P1 | 1 | DF40C-20DP-0.4V(51) | Hirose Electric Co Ltd | DF40C-20-DP | Connector, HDR, 20Pos, 0.4mm, SMD, GOLD |  | DF40C-20DP-0.4V(51)
 |  | PCB0004 | 1 |  |  |  | IMU PCB |  | PCB0004
 |  | R2, R3, R4, R5 | 4 | ESR03EZPJ5R1 | Rohm Semiconductor | R0603 | RES SMD 5.1 OHM 5% 1/4W 0603 |  | 5R5, 5R5, 5R5, 2.2R
 |  | U1 | 1 | L3GD20 | STMICROELECTRONICS | L3GD20 | Sensor, Low-power, Three-axis, Angular rate
 |  | U2 | 1 | LSM303DTR | STMicroelectronics | LSM303D | Module, 3D Accelerometer, 3D Magnetometer
 |  | U3_A | 1 | MPU-9250 | InvenSense | MPU-9250
 |  | U4 | 1 | MS561101BA03-50 | Measurement Specialties | MS5611-01BA | Board, Digital pressure sensor I2C/SPI
Remark:
This form is used for both first Engineering BOM entry request and BOM change update request, if it is for BOM change, engineer needs to fill in the 'Change History' column as well as update the 'Full BOM' column .
ECN No. will be provided by PCH, date code should be included, e.g. release on 30 Oct.,2014, the ECN No. is ECN20141030xxxx
Action: A-Add Part; D-Delete Part; M-Modify part property e.g description, qty, material etc.

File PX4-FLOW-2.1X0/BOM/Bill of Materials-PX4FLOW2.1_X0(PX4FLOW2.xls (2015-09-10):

Manufacturer 1 | Manufacturer Part Number 1 | Supplier Part Number 1 | 3DR_PARTNO | Description | Designator | Value | Quantity | Footprint | Mfg Part Num (Alternate) | Mfg Name (Alternate) | Supplier Unit Price 1 | Total Cost per
Yageo | CC0402ZRY5V7BB104 | 311-1047-1-ND |  | CapacitorStandard 0603 ceramic capacitor, and 0.1" leaded capacitor., CapacitorStandard 0603 ceramic capacitor, and 0.1" leaded capacitor., CapacitorStandard 0603 ceramic capacitor, and 0.1" leaded capacitor., CapacitorStandard 0603 ceramic capacitor, and 0.1" leaded capacitor., CapacitorStandard 0603 ceramic capacitor, and 0.1" leaded capacitor., CapacitorStandard 0603 ceramic capacitor, and 0.1" leaded capacitor., CapacitorStandard 0603 ceramic capacitor, and 0.1" leaded capacitor., CapacitorStandard 0603 ceramic capacitor, and 0.1" leaded capacitor., CapacitorStandard 0603 ceramic capacitor, and 0.1" leaded capacitor., CapacitorStandard 0603 ceramic capacitor, and 0.1" leaded capacitor., CapacitorStandard 0603 ceramic capacitor, and 0.1" leaded capacitor., CapacitorStandard 0603 ceramic capacitor, and 0.1" leaded capacitor., CapacitorStandard 0603 ceramic capacitor, and 0.1" leaded capacitor., CapacitorStandard 0603 ceramic capacitor, and 0.1" leaded capacitor., CapacitorStandard 0603 ceramic capacitor, and 0.1" leaded capacitor., CapacitorStandard 0603 ceramic capacitor, and 0.1" leaded capacitor., CapacitorStandard 0603 ceramic capacitor, and 0.1" leaded capacitor., CapacitorStandard 0603 ceramic capacitor, and 0.1" leaded capacitor., CapacitorStandard 0603 ceramic capacitor, and 0.1" leaded capacitor., CapacitorStandard 0603 ceramic capacitor, and 0.1" leaded capacitor., CapacitorStandard 0603 ceramic capacitor, and 0.1" leaded capacitor., 0402 | C1, C2, C5, C7, C8, C9, C10, C15, C16, C17, C18, C19, C20, C21, C22, C23, C28, C29, C30, C31, C32, C35 |  | 22 | C0402 |  |  | $0.00242 | $0.05
TDK Corporation | C1005C0G1H080C050BA | 445-4890-1-ND | ECM0710 | CAP CER 8PF 50V C0G 0402 | C3, C4 | 8p | 2 | 0402-CAP |  |  | $0.01 | $0.01
TDK Corporation | C3216X5R1A107M160AC | 445-6007-1-ND | ECM0716 | CAP CER 100UF 10V 20% X5R 1206 | C6, C14, C36 | 100U | 3 | 1206-CAP |  |  | $0.63 | $1.88
TDK Corporation | C1608X6S1C225K080AC | 445-7438-1-ND | ECM0619 | Capacitor, 2.2uF, 16V, 10%, X6S, 0603, Ceramic | C11, C12, C27, C34 | 2u2 | 4 | 0603-CAP |  |  | $0.06 | $0.22
Yageo | CC0402KRX7R9BB471 | 311-1028-1-ND |  | CapacitorStandard 0603 ceramic capacitor, and 0.1" leaded capacitor. | C13 |  | 1 | C0402 |  |  | $0.00249 | $0.00249
Murata Electronics North America | GRM155R71C103KA01D | 490-1313-1-ND |  | CapacitorStandard 0603 ceramic capacitor, and 0.1" leaded capacitor. | C24 |  | 1 | C0402 |  |  | $0.00451 | $0.00451
Yageo | CC0402KRX7R7BB103 | 311-1042-1-ND |  | CapacitorStandard 0603 ceramic capacitor, and 0.1" leaded capacitor. | C25 |  | 1 | C0402 |  |  | $0.00249 | $0.00249
Murata Electronics North America | GRM155R71C102KA01D | 490-6325-1-ND |  | CapacitorStandard 0603 ceramic capacitor, and 0.1" leaded capacitor. | C26 |  | 1 | C0402 |  |  | $0.00451 | $0.00451
Yageo | CC0402ZRY5V7BB104 | 311-1047-1-ND | ECM0700 | Capacitor, 0.1uF, 16V, Y5V, 0402, Ceramic, CAP CER 0.1UF 16V Y5V 0402 | C33, C3004 | 0u1 | 2 | 0402-CAP |  |  | $0.00242 | $0.00484
Vishay Semiconductor Diodes Division | MSS1P4-M3/89A | MSS1P4-M3/89AGICT-ND |  | Schottky barrier diode in DO214AC, e.g. Fairchild SS14. | D1 |  | 1 | MICROSMP |  |  | $0.08 | $0.08
TE Connectivity / Raychem | PESD0402-140 | 650-PESD0402-140 | ECM0837 | Diode, TVS, 14VWM, 40VC, 0402, SMD | D104, D108 |  | 2 | 0402-TVS |  |  | $0.09 | $0.19
Taiyo Yuden | BKP1005HS121-TV | 587-3954-1-ND |  | FERRITE BEAD 120 OHM 0402 | L2, L11 |  | 2 | L0402 |  |  | $0.03 | $0.06
Taiyo Yuden | BKP1005HS121-TV | 587-3954-1-ND |  |  | L8 |  | 1 | L0402 |  |  | $0.03 | $0.03
AVX Corp/Kyocera Corp | KNH16C104DA5TS | 478-6878-1-ND | ECM0719 | Capacitor, Filter, 0.1uF, 25V, 2A, 0603, SMD | L103, L106 |  | 2 | KYOCERA-KNH16-DA |  |  | $0.09 | $0.17
Panasonic Electronic Components | LNJ337W83RA | LNJ337W83RACT-ND |  | Green LED | LED1 |  | 1 | LED-0603 |  |  | $0.09 | $0.09
ON Semiconductor | NTGS4111PT1G | NTGS4111PT1GOSCT-ND |  |  | Q1 |  | 1 | TSOP-6 |  |  | $0.14 | $0.14
Yageo | RC0402FR-071K5L | 311-1.50KLRCT-ND | ECM0803 | RES 1.5K OHM 1/16W 1% 0402 SMD | R1, R2, R3002, R3004 | 1K5 | 4 | R0402 |  |  | $0.00176 | $0.01
Stackpole Electronics Inc. | RMCF0402JT100R | RMCF0402JT100RCT-ND |  | ResistorBasic schematic elements and footprints for 0603, 1206, and PTH 1/10th watt (small) resistors. | R3, R4 |  | 2 | R0402 |  |  | $0.00171 | $0.00342
Yageo | RC0402FR-0710KL | 311-10.0KLRCT-ND | ECM0800 | RES 10K OHM 1/16W 1% 0402 SMD | R5, R7, R16, R18 | 10K | 4 | R0402 |  |  | $0.00176 | $0.01
Stackpole Electronics Inc. | RMCF0402JT22R0 | RMCF0402JT22R0CT-ND |  | ResistorBasic schematic elements and footprints for 0603, 1206, and PTH 1/10th watt (small) resistors. | R6, R8 |  | 2 | R0402 |  |  | $0.00171 | $0.00342
Rohm Semiconductor | MCR01MZPJ271 | RHM270JCT-ND |  | ResistorBasic schematic elements and footprints for 0603, 1206, and PTH 1/10th watt (small) resistors. | R9 |  | 1 | R0402 |  |  | $0.00238 | $0.00238
Stackpole Electronics Inc. | RMCF0402JT470R | RMCF0402JT470RCT-ND |  | ResistorBasic schematic elements and footprints for 0603, 1206, and PTH 1/10th watt (small) resistors. | R12 |  | 1 | R0402 |  |  | $0.00171 | $0.00171
Rohm Semiconductor | MCR01MZPJ271 | RHM270JCT-ND |  | ResistorBasic schematic elements and footprints for 0603, 1206, and PTH 1/10th watt (small) resistors. | R13 |  | 1 | R0402 |  |  | $0.00238 | $0.00238
Panasonic Electronic Components | ERJ-PA3F68R0V | P68.00BYCT-ND |  | RES SMD 68 OHM 1% 1/4W 0603 | R14 |  | 1 | 0603-RES |  |  | $0.02 | $0.02
Susumu | RL0816S-5R6-F | 408-1437-2-ND |  | RES SMD 5.6 OHM 1% 1/5W 0603 | R15, R17 |  | 2 | 0603-RES |  |  | $0.05 | $0.11
Stackpole Electronics Inc. | RMCF0402JT1K00 | RMCF0402JT1K00CT-ND |  | ResistorBasic schematic elements and footprints for 0603, 1206, and PTH 1/10th watt (small) resistors. | R19, R20 |  | 2 | R0402 |  |  | $0.00171 | $0.00342
Yageo | RC0402FR-07120RL | 311-120LRCT-ND | ECM0820 | RES 120 OHM 1/16W 1% 0402 SMD | R3010 | 120R | 1 | R0402 |  |  | $0.00176 | $0.00176
Micrel Inc. | MIC5207-3.3YM5 TR | 576-1267-1-ND |  | Voltage Regulator LDOStandard 150mA LDO voltage regulator in SOT-23 layout. Micrel part MIC5205. BP (by-pass) pin is used to lower output noise with 470pF cap. | U1 |  | 1 | SOT23-5 |  |  | $0.30 | $0.30
STMICROELECTRONICS | STM32F427VIT7TR | 19X6230 |  | ARM Cortex-M4 32-bit MCU+FPU, 210 DMIPS, 2048 kB Flash, 256 kB Internal RAM, 82 I/Os, 100-pin LQFP, -40 to 105 degC, Tape and Reel | U2 |  | 1 | STM-LQFP100_N |  |  | $10.63 | $10.63
OSRAM Opto Semiconductors Inc. | LRTB GFTG-T7AW-1+V7A7-29+R5T9-49-L | 475-2822-1-ND |  | RGB LED with separate anode/cathode terminals | U3 |  | 1 | 6-PLCC |  |  | $0.00 | $0.00
Microchip Technology | 24FC128T-I/MS | 24FC128T-I/MS-ND |  | I2C EEPROM Generic footprint for I2C EEPROMS. Compatible types include: Microchip 24FC128-I/MS Microchip 24AA256-I/MS ST Microelectronics M24128-BWDW6TP | U8 |  | 1 | MSOP-8 |  |  | $0.51 | $0.51
STMICROELECTRONICS | L3GD20 | 73T0644 | ECM0827 | Sensor, Low-power, Three-axis, Angular rate | U12 |  | 1 | L3GD20 |  |  | $3.30 | $3.30
InvenSense | MPU-9250 | 1428-1019-1-ND |  |  | U405 |  | 1 | MPU-6500 |  |  | $6.13 | $6.13
Maxim Integrated | MAX3051EKA+T | MAX3051EKA+TCT-ND | ECM0831 | IC TXRX CAN 1MBPS SOT23-8 | U3004 | CAN | 1 | SOT23-8 |  |  | $1.93 | $1.93
Aptina-ON Semiconductor | MT9V034C12STM | 557-1454-ND |  |  | U$5 |  | 1 | CLCC-48 |  |  | $0.00 | $0.00
NDK | NX3225SA-24.000MHZ-STD-CSR-1 | 644-1052-1-ND | ECM0708 | CRYSTAL 24MHZ 8PF SMD | X1 | 24MHz | 1 | OSCILLATOR-3.2X2.5 |  |  | $0.39 | $0.39
 |  |  |  |  |  |  |  |  |  |  |  | $0.00
 |  |  |  |  |  |  |  |  |  |  |  | $0.00
 |  |  |  |  |  |  |  |  |  |  |  | $0.00
 |  |  |  |  |  |  |  |  |  |  |  | $0.00
 |  |  |  |  |  |  |  |  |  |  |  | $0.00
 |  |  |  |  |  |  |  |  |  |  |  | $0.00
 |  |  |  |  |  |  |  |  |  |  |  | $0.00
 |  |  |  |  |  |  |  |  |  |  |  | $0.00
 |  |  |  |  |  |  |  |  |  |  |  | $0.00
 |  |  |  |  |  |  |  |  |  |  |  | $0.00
 |  |  |  |  |  |  |  |  |  |  |  | $0.00
 |  |  |  |  |  |  |  |  |  |  |  | $0.00
 |  |  |  |  |  |  |  |  |  |  |  | $0.00
 |  |  |  |  |  |  |  |  |  |  |  | $0.00
 |  |  |  |  |  |  |  |  |  |  |  | $0.00
 |  |  |  |  |  |  |  |  |  |  |  | $0.00
 |  |  |  |  |  |  |  |  |  |  |  | $0.00
 |  |  |  |  |  |  |  |  |  |  |  | $0.00
 |  |  |  |  |  |  |  |  |  |  |  | $0.00
 |  |  |  |  |  |  |  |  |  |  |  | $0.00
 |  |  |  |  |  |  |  |  |  |  |  | $0.00
 |  |  |  |  |  |  |  |  |  |  |  | $0.00
 |  |  |  |  |  |  |  |  |  |  |  | $0.00
 |  |  |  |  |  |  |  |  |  |  |  | $0.00
 |  |  |  |  |  |  |  |  |  |  |  | $0.00
 |  |  |  |  |  |  |  |  |  |  |  | $0.00
 |  |  |  |  |  |  |  |  |  |  |  | $0.00
 |  |  |  |  |  |  |  |  |  |  |  | $0.00
 |  |  |  |  |  |  |  |  |  |  |  | $0.00
 |  |  |  |  |  |  |  |  |  |  |  | $0.00
 |  |  |  |  |  |  |  |  |  |  |  | $0.00
 |  |  |  |  |  | Total Qty. | 77 |  |  |  | Total Cost | $26.29
 |  |  |  |  |  | APPROVALS
PART NUMBER (3DR ERP) | BOM REVISION | REV. DATE |  | REF. DRAWING/SCHEMATIC: |  | Dept. | Name | Signature | Date
PX4FLOW2.1_X0 |  | 10/09/2015 |  | PX4FLOW2.1_X0.PrjPcb |  | Design Engineering (PR)
PRODUCT DESCRIPTION | ECR/ECO/ECN |  |  |  |  | Dir. Of Eng. | Tim M.
PX4FLOW2.1_X0.PrjPcb |  | Parts Info: |  | N/A |  | Operations Mgmt | Lorenzo L.
Total parts = | 77 | Unique Parts: |  | N/A |  | Production | Juan V.
Feeder requirement: | N/A | Total Placements: 0 |  | N/A

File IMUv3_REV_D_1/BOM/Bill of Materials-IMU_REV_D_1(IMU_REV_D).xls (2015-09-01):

Manufacturer 1 | Manufacturer Part Number 1 | Supplier Part Number 1 | 3DR_PARTNO | Description | Designator | Value | Quantity | Footprint | Mfg Part Num (Alternate) | Mfg Name (Alternate) | Supplier Unit Price 1 | Total Cost per
Yageo | CC0805ZKY5V6BB106 | 311-1355-1-ND | ECM0713 | Capacitor, 10uF, 10V, Y5V, 0805, Ceramic | C1, C4, C6, C13 | 10u | 4 | 0805-CAP |  |  | $0.03 | $0.12
Yageo | CC0402ZRY5V7BB104 | 311-1047-1-ND | ECM0700 | Capacitor, 0.1uF, 16V, Y5V, 0402, Ceramic | C2, C5, C10, C12, C14 | 0u1 | 5 | 0402-CAP |  |  | $0.00257 | $0.01
Yageo | CC0402KRX7R7BB103 | 311-1042-1-ND | ECM0711 | Capacitor, 10000pF, 16V, 10%, X7R, 0402, Ceramic | C3 | 10000pF | 1 | 0402-CAP |  |  | $0.00265 | $0.00265
TDK Corporation | C1005X5R1C474K050BC | 445-4976-1-ND | ECM0704 | Capacitor, 0.47uF, 16V, 10%, X5R, 0402, Ceramic | C7 | 0u47 | 1 | 0402-CAP |  |  | $0.02 | $0.02
TDK Corporation | C1608X6S1C225K080AC | 445-7438-1-ND | ECM0619 | Capacitor, 2.2uF, 16V, 10%, X6S, 0603, Ceramic | C8, C9 | 2u2 | 2 | 0603-CAP |  |  | $0.06 | $0.12
AVX Corporation | 06033C103JAT2A | 478-7901-1-ND | ECM0620 | Capacitor, 10000pF, 25V, 5%, X7R, 0603, Ceramic | C11 | 10000pF | 1 | 0603-CAP |  |  | $0.06 | $0.06
PennEngineering | PEM-SMTSO-M1.6-2-ET | PEM-SMTSO-M1.6-2-ET | PRT0438 | Fastener, M1.6x2mm, SMTSO, Carbon Steel | Nut 1, Nut 2, Nut 3, Nut 4 |  | 4 | PEM-SMTSO-M1.6-2-ET |  |  | $0.70 | $2.80
Hirose Electric Co Ltd | DF40C-20DP-0.4V(51) | H11618CT-ND | ECM0510 | Connector, HDR, 20Pos, 0.4mm, SMD, GOLD | P1 | DF40C-20DP-0.4V(51) | 1 | DF40C-20-DP |  |  | $0.37 | $0.37
 |  |  | PCB0004 | IMU PCB | PCB0004 | PCB0004 | 1 |  |  |  |  | $0.00
STMICROELECTRONICS | L3GD20 | 73T0644 | ECM0827 | Sensor, Low-power, Three-axis, Angular rate | U1 |  | 1 | L3GD20 |  |  | $3.22 | $3.22
STMicroelectronics | LSM303DTR | 497-13819-1-ND | ECM0828 | Module, 3D Accelerometer, 3D Magnetometer | U2 |  | 1 | LSM303D |  |  | $1.59 | $1.59
InvenSense | MPU-6000 | 1428-1005-1-ND | ECM0834 | 3 Axis Accel, 3Axis Gyro | U3 |  | 1 | QFN-24 |  |  | $5.50 | $5.50
Measurement Specialties | MS561101BA03-50 | 824-MS561101BA03-50 | ECM0835 | Board, Digital pressure sensor I2C/SPI | U4 |  | 1 | MS5611-01BA |  |  | $6.62 | $6.62
 |  |  |  |  |  |  |  |  |  |  |  | $0.00
 |  |  |  |  |  |  |  |  |  |  |  | $0.00
 |  |  |  |  |  |  |  |  |  |  |  | $0.00
 |  |  |  |  |  |  |  |  |  |  |  | $0.00
 |  |  |  |  |  |  |  |  |  |  |  | $0.00
 |  |  |  |  |  |  |  |  |  |  |  | $0.00
 |  |  |  |  |  |  |  |  |  |  |  | $0.00
 |  |  |  |  |  |  |  |  |  |  |  | $0.00
 |  |  |  |  |  |  |  |  |  |  |  | $0.00
 |  |  |  |  |  |  |  |  |  |  |  | $0.00
 |  |  |  |  |  |  |  |  |  |  |  | $0.00
 |  |  |  |  |  |  |  |  |  |  |  | $0.00
 |  |  |  |  |  |  |  |  |  |  |  | $0.00
 |  |  |  |  |  |  |  |  |  |  |  | $0.00
 |  |  |  |  |  |  |  |  |  |  |  | $0.00
 |  |  |  |  |  |  |  |  |  |  |  | $0.00
 |  |  |  |  |  |  |  |  |  |  |  | $0.00
 |  |  |  |  |  |  |  |  |  |  |  | $0.00
 |  |  |  |  |  |  |  |  |  |  |  | $0.00
 |  |  |  |  |  |  |  |  |  |  |  | $0.00
 |  |  |  |  |  |  |  |  |  |  |  | $0.00
 |  |  |  |  |  |  |  |  |  |  |  | $0.00
 |  |  |  |  |  |  |  |  |  |  |  | $0.00
 |  |  |  |  |  |  |  |  |  |  |  | $0.00
 |  |  |  |  |  |  |  |  |  |  |  | $0.00
 |  |  |  |  |  |  |  |  |  |  |  | $0.00
 |  |  |  |  |  |  |  |  |  |  |  | $0.00
 |  |  |  |  |  |  |  |  |  |  |  | $0.00
 |  |  |  |  |  |  |  |  |  |  |  | $0.00
 |  |  |  |  |  |  |  |  |  |  |  | $0.00
 |  |  |  |  |  |  |  |  |  |  |  | $0.00
 |  |  |  |  |  | Total Qty. | 24 |  |  |  | Total Cost | $20.44
 |  |  |  |  |  | APPROVALS
PART NUMBER (3DR ERP) | BOM REVISION | REV. DATE |  | REF. DRAWING/SCHEMATIC: |  | Dept. | Name | Signature | Date
IMU_REV_D |  | 12/08/2015 |  | IMU_REV_D_1.PrjPcb |  | Design Engineering (PR)
PRODUCT DESCRIPTION | ECR/ECO/ECN |  |  |  |  | Dir. Of Eng. | Tim M.
IMU_REV_D_1.PrjPcb |  | Parts Info: |  | N/A |  | Operations Mgmt | Lorenzo L.
Total parts = | 24 | Unique Parts: |  | N/A |  | Production | Juan V.
Feeder requirement: | N/A | Total Placements: 0 |  | N/A

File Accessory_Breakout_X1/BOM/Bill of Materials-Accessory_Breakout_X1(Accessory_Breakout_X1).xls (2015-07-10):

Manufacturer 1 | Manufacturer Part Number 1 | Supplier Part Number 1 | 3DR_PARTNO | Description | Designator | Value | Quantity | Footprint | Mfg Part Num (Alternate) | Mfg Name (Alternate) | Supplier Unit Price 1 | Total Cost per
ON Semiconductor | MMSZ5232BT1G | MMSZ5232BT1GOSCT-ND | ECM0536 | DIODE ZENER 5.6V 500MW SOD123 | D4 | 5.6V | 1 | SOD-123 |  |  | $0.05 | $0.05
JAE Electronics | TX24-30R-6ST-N1E | 656-TX2430R6STN1E |  |  | J1 |  | 1 | JAE TX24 |  |  | $0.66 | $0.66
Molex Inc | 0473460001 | WM17141DKR-ND | ECM0486 | MICRO USB B, BOTTOM MOUNT | J2001 |  | 1 | MOLEX-47346-0001 |  |  | $0.57 | $0.57
Molex Inc | 5023820470 | WM4781CT-ND | PRT0441 | Connector, Rcpt, 4Pos, 1.25MM, W/B, VERT, SMD, Tin | P3 |  | 1 | CLICKMATE_V4 |  |  | $0.73 | $0.73
Molex Inc | 5023820670 | WM4783CT-ND | PRT0439 | Connector, Rcpt, 6Pos, 1.25MM, W/B, VERT, SMD, Tin | P4 |  | 1 | CLICKMATE_V6 |  |  | $0.87 | $0.87
JST Sales America Inc | SM06B-SURS-TF(LF)(SN) | SM06B-SURS-TF(LF)(SN)-ND | PRT0442 | Connector, Header, 6Pos, .8mm IDC, R/A, SMD, Tin | P5, P6 |  | 2 | JST_SUR_H6 |  |  | $0.43 | $0.86
 |  |  |  |  |  |  |  |  |  |  |  | $0.00
 |  |  |  |  |  |  |  |  |  |  |  | $0.00
 |  |  |  |  |  |  |  |  |  |  |  | $0.00
 |  |  |  |  |  |  |  |  |  |  |  | $0.00
 |  |  |  |  |  |  |  |  |  |  |  | $0.00
 |  |  |  |  |  |  |  |  |  |  |  | $0.00
 |  |  |  |  |  |  |  |  |  |  |  | $0.00
 |  |  |  |  |  |  |  |  |  |  |  | $0.00
 |  |  |  |  |  |  |  |  |  |  |  | $0.00
 |  |  |  |  |  |  |  |  |  |  |  | $0.00
 |  |  |  |  |  |  |  |  |  |  |  | $0.00
 |  |  |  |  |  |  |  |  |  |  |  | $0.00
 |  |  |  |  |  |  |  |  |  |  |  | $0.00
 |  |  |  |  |  |  |  |  |  |  |  | $0.00
 |  |  |  |  |  |  |  |  |  |  |  | $0.00
 |  |  |  |  |  |  |  |  |  |  |  | $0.00
 |  |  |  |  |  |  |  |  |  |  |  | $0.00
 |  |  |  |  |  |  |  |  |  |  |  | $0.00
 |  |  |  |  |  |  |  |  |  |  |  | $0.00
 |  |  |  |  |  |  |  |  |  |  |  | $0.00
 |  |  |  |  |  |  |  |  |  |  |  | $0.00
 |  |  |  |  |  |  |  |  |  |  |  | $0.00
 |  |  |  |  |  |  |  |  |  |  |  | $0.00
 |  |  |  |  |  |  |  |  |  |  |  | $0.00
 |  |  |  |  |  |  |  |  |  |  |  | $0.00
 |  |  |  |  |  |  |  |  |  |  |  | $0.00
 |  |  |  |  |  |  |  |  |  |  |  | $0.00
 |  |  |  |  |  |  |  |  |  |  |  | $0.00
 |  |  |  |  |  |  |  |  |  |  |  | $0.00
 |  |  |  |  |  |  |  |  |  |  |  | $0.00
 |  |  |  |  |  |  |  |  |  |  |  | $0.00
 |  |  |  |  |  | Total Qty. | 7 |  |  |  | Total Cost | $3.74
 |  |  |  |  |  | APPROVALS
PART NUMBER (3DR ERP) | BOM REVISION | REV. DATE |  | REF. DRAWING/SCHEMATIC: |  | Dept. | Name | Signature | Date
Accessory_Breakout_X1 |  | 10/07/2015 |  | Accessory_Breakout_X1.PrjPcb |  | Design Engineering (PR)
PRODUCT DESCRIPTION | ECR/ECO/ECN |  |  |  |  | Dir. Of Eng.
Accessory_Breakout_X1.PrjPcb |  | Parts Info: |  | N/A |  | Operations Mgmt
Total parts = | 7 | Unique Parts: |  | N/A |  | Production
Feeder requirement: | N/A | Total Placements: 0 |  | N/A

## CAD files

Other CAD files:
PX4_FLOW2.0_X0/3D/C33.sldasm
PX4_FLOW2.0_X0/3D/U405.sldasm
PX4_FLOW2.0_X0/3D/R8.sldasm
PX4_FLOW2.0_X0/3D/P1.sldasm
PX4_FLOW2.0_X0/3D/R3002.sldasm
PX4_FLOW2.0_X0/3D/D104.sldasm
PX4_FLOW2.0_X0/3D/R2.sldasm
PX4_FLOW2.0_X0/3D/R3004.sldasm
PX4_FLOW2.0_X0/3D/L106.sldasm
PX4_FLOW2.0_X0/3D/R9.sldasm
PX4_FLOW2.0_X0/3D/U$8.sldasm
PX4_FLOW2.0_X0/3D/C12.sldasm
PX4_FLOW2.0_X0/3D/R10.sldasm
PX4_FLOW2.0_X0/3D/R6.sldasm
PX4_FLOW2.0_X0/3D/R7.sldasm
PX4_FLOW2.0_X0/3D/LIDAR.sldasm
PX4_FLOW2.0_X0/3D/C34.sldasm
PX4_FLOW2.0_X0/3D/R3010.sldasm
IMUv3_REV_D/IMU_REV_D.DXF
PX4-FLOW-2.1X0/PX4FLOW2.1_X0.DXF
PX4_FLOW2.0_X0/3D/1510510464.sldasm
PX4_FLOW2.0_X0/3D/473460001.sldasm
PX4_FLOW2.0_X0/3D/5023820470.sldasm
PX4_FLOW2.0_X0/3D/5023820670.sldasm
PX4_FLOW2.0_X0/3D/Board.sldprt
PX4_FLOW2.0_X0/3D/C11.sldasm
PX4_FLOW2.0_X0/3D/C27.sldasm
PX4_FLOW2.0_X0/3D/C3004.sldasm
PX4_FLOW2.0_X0/3D/D108.sldasm
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

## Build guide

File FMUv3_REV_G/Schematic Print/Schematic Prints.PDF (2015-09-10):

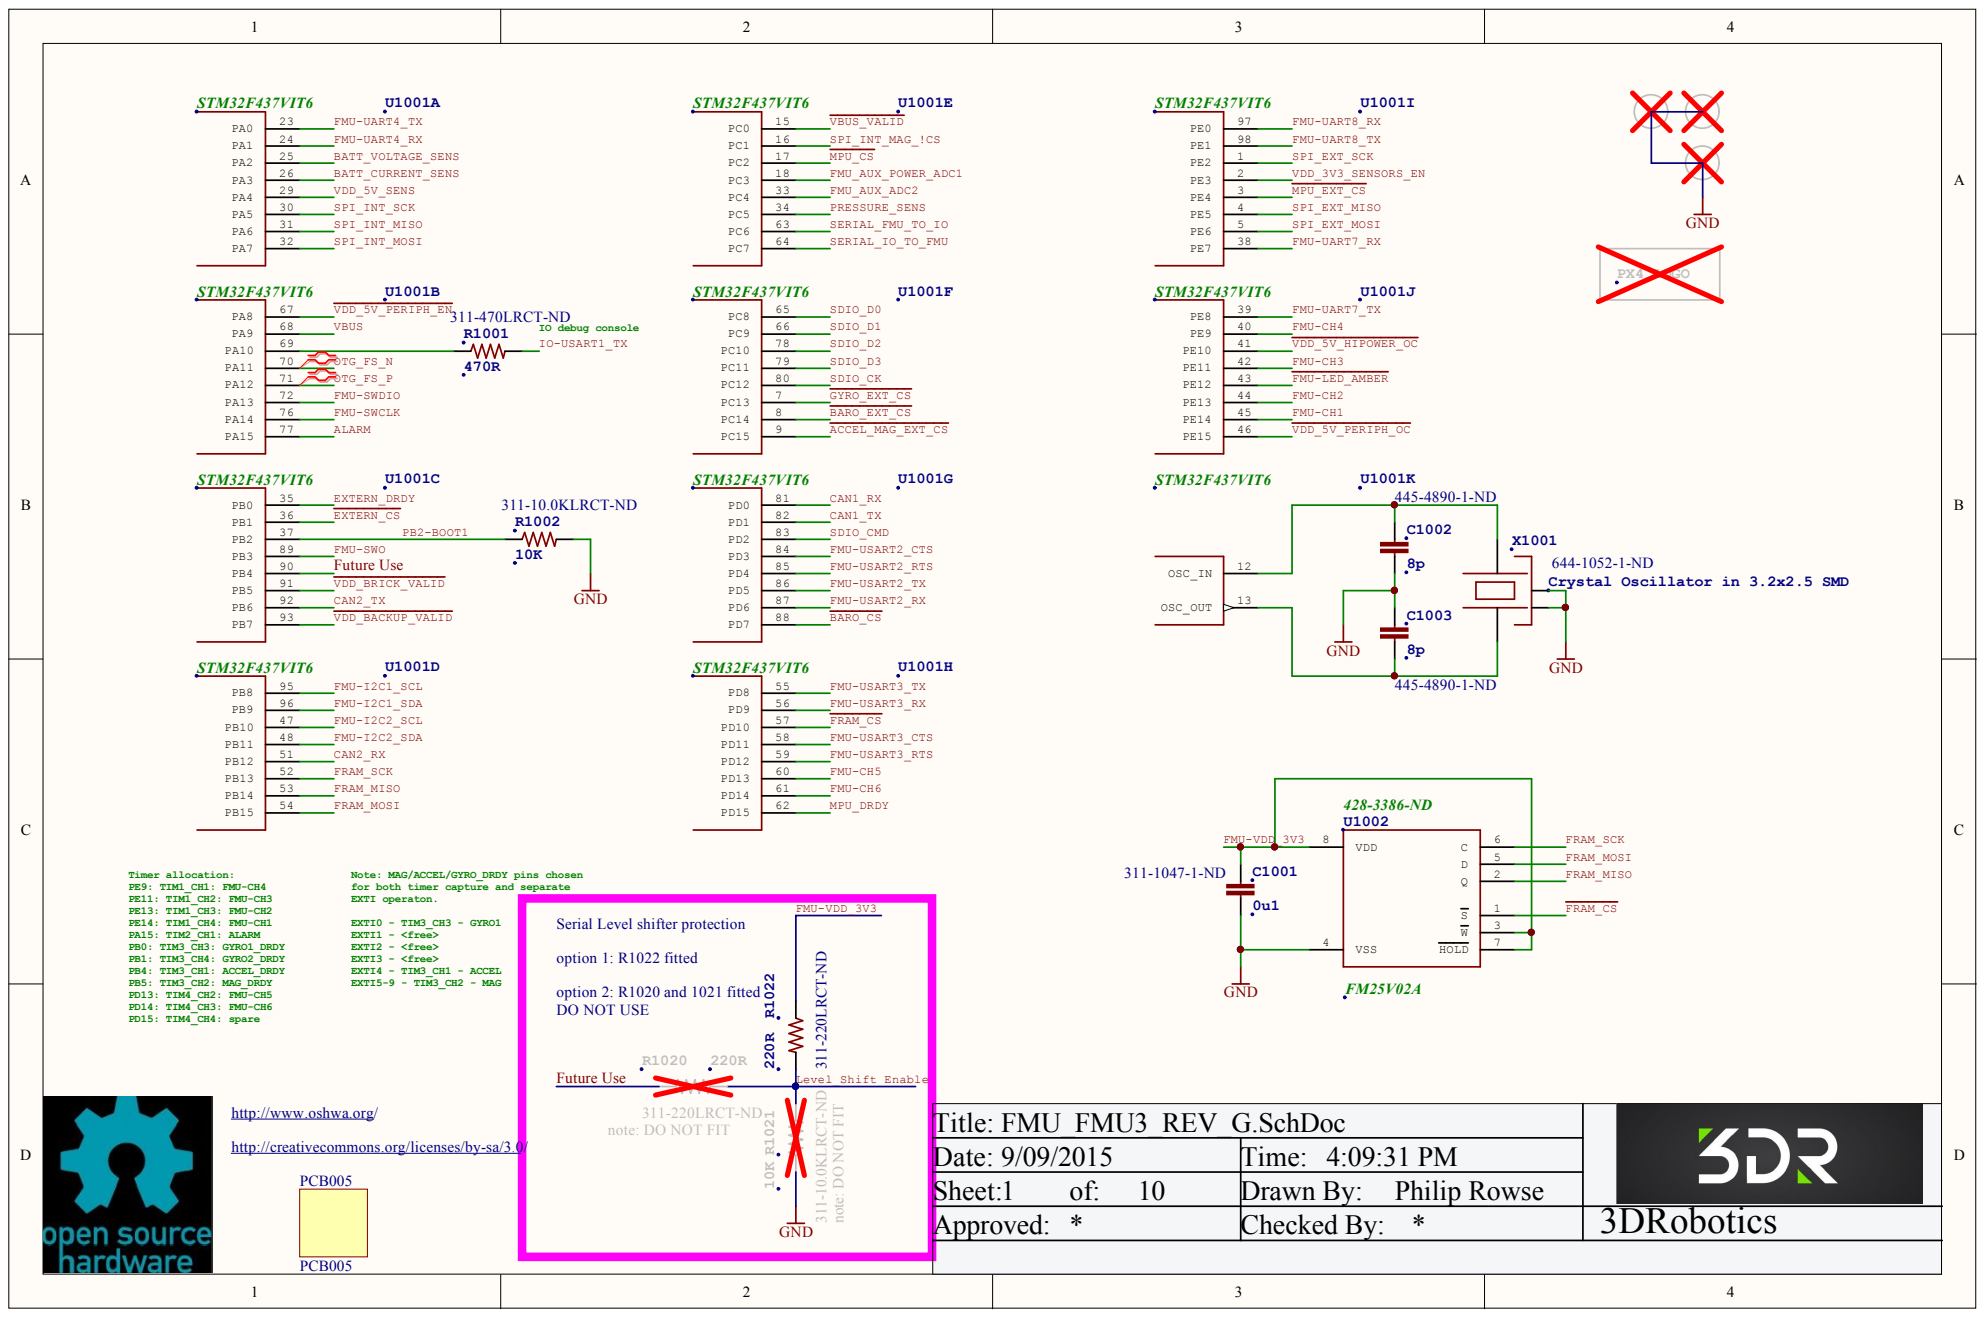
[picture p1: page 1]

Note: MAG/ACCEL/GYRO_DRDY pins chosen
for both timer capture and separate
EXTI operaton.

Serial Level shifter protection

http://www.oshwa.org/

311-220LRCT-ND
note: DO NOT FIT

Title: FMU_FMU3_REV_G.SchDoc
Date: 9/09/2015 | Time: 4:09:31 PM
Sheet:1 of: 10 | Drawn By: Philip Rowse
Approved: * | Checked By: * | 3DRobotics

http://creativecommons.org/licenses/by-sa/3.0/

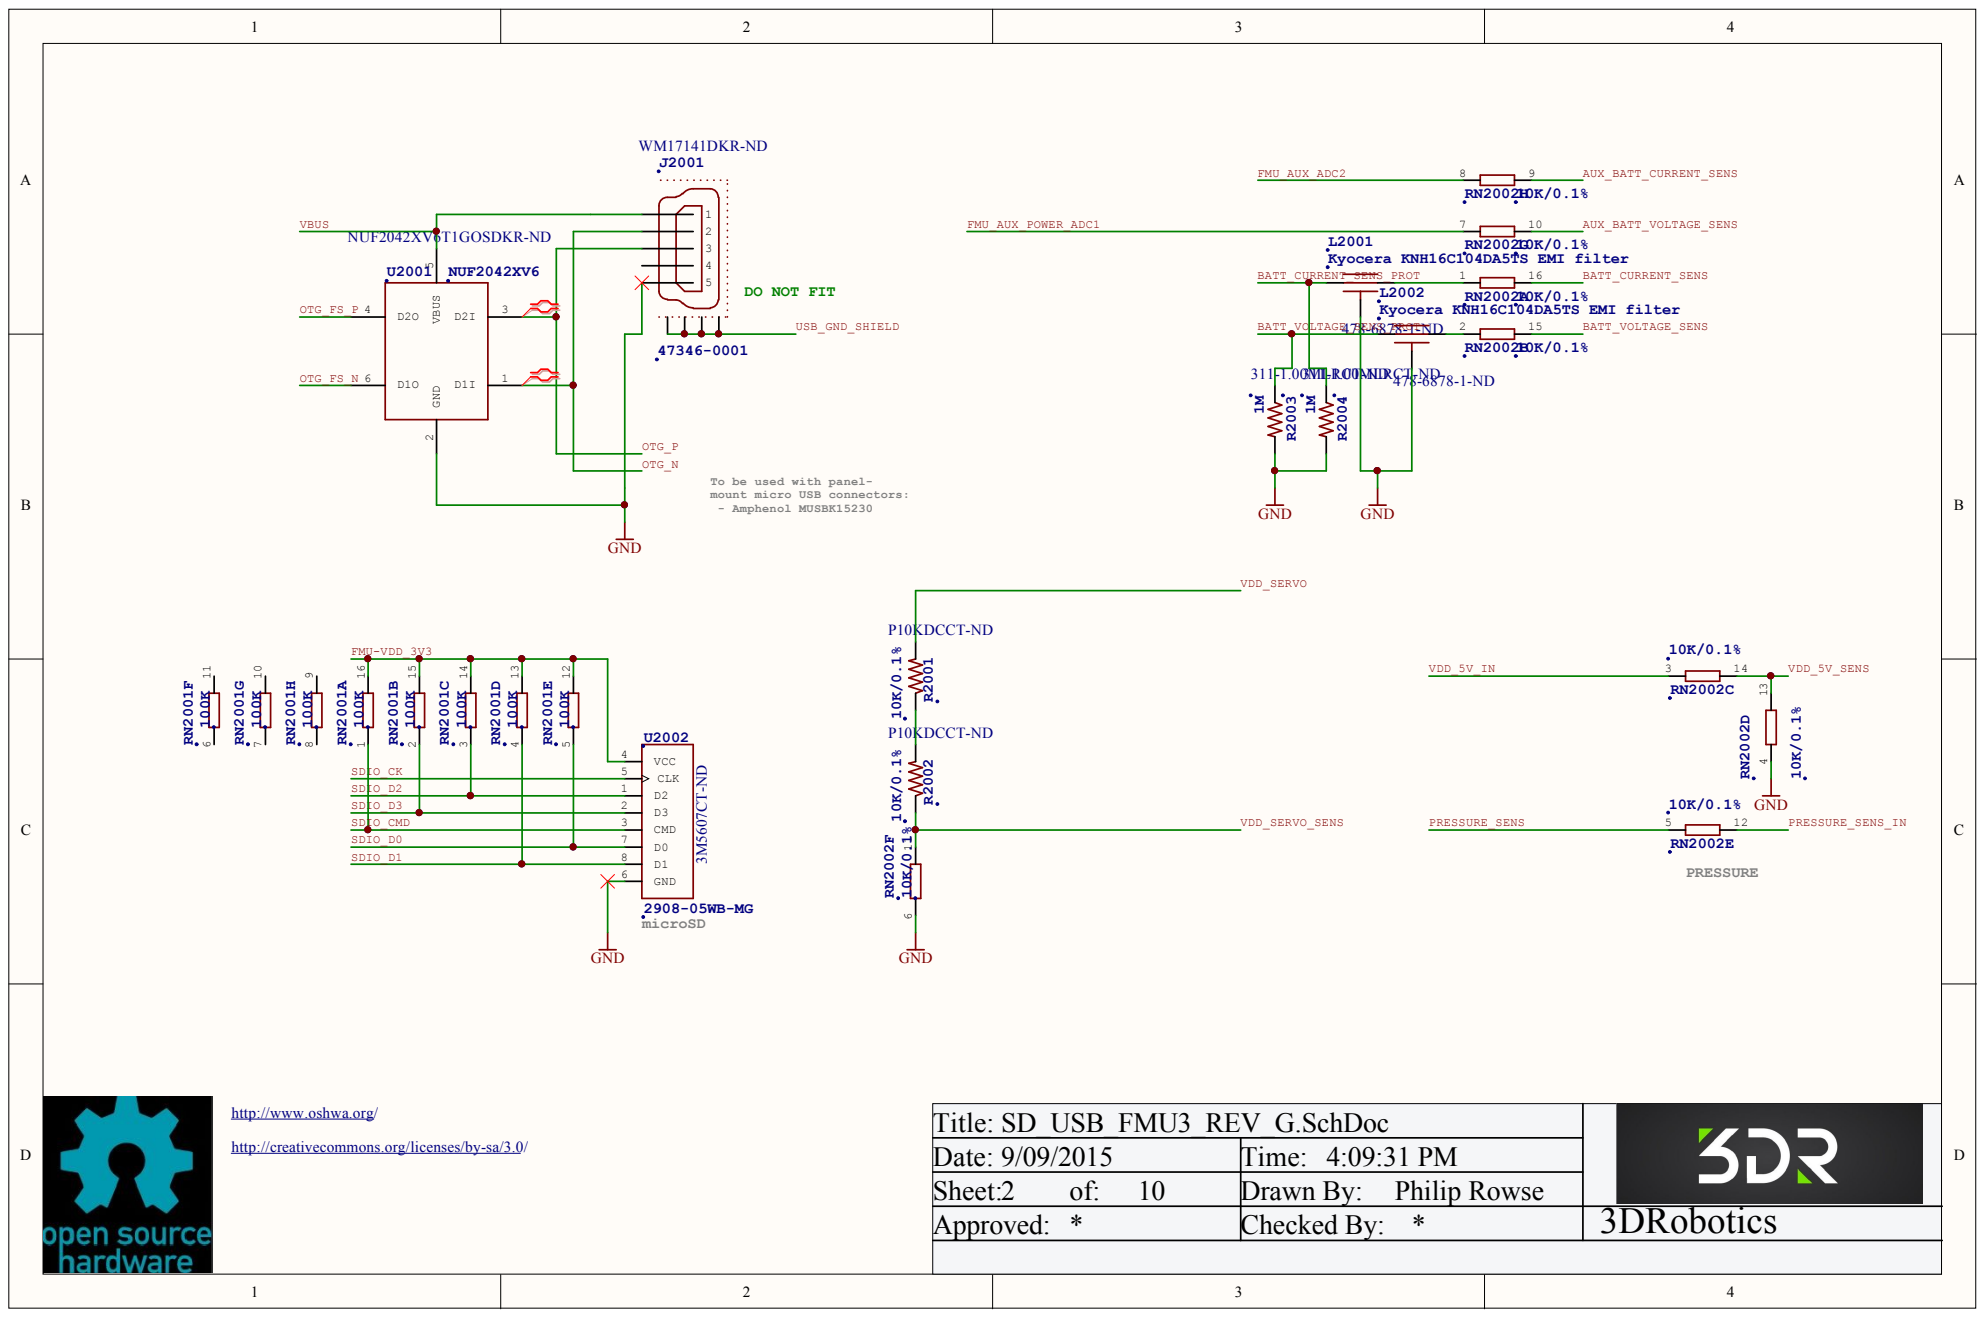
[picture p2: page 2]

Kyocera KNH16C104DA5TS EMI filter 478-6878-1-ND

Title: SD_USB_FMU3 _REV_G.SchDo c
Date: 9/0 9/2 0 1 5 | Time: 4:0 9:3 1 PM
Sheet: 2 of: 1 0 | Drawn By : Philip Rowse
Ap pro ved : * | Checked By : * | 3DRobotics

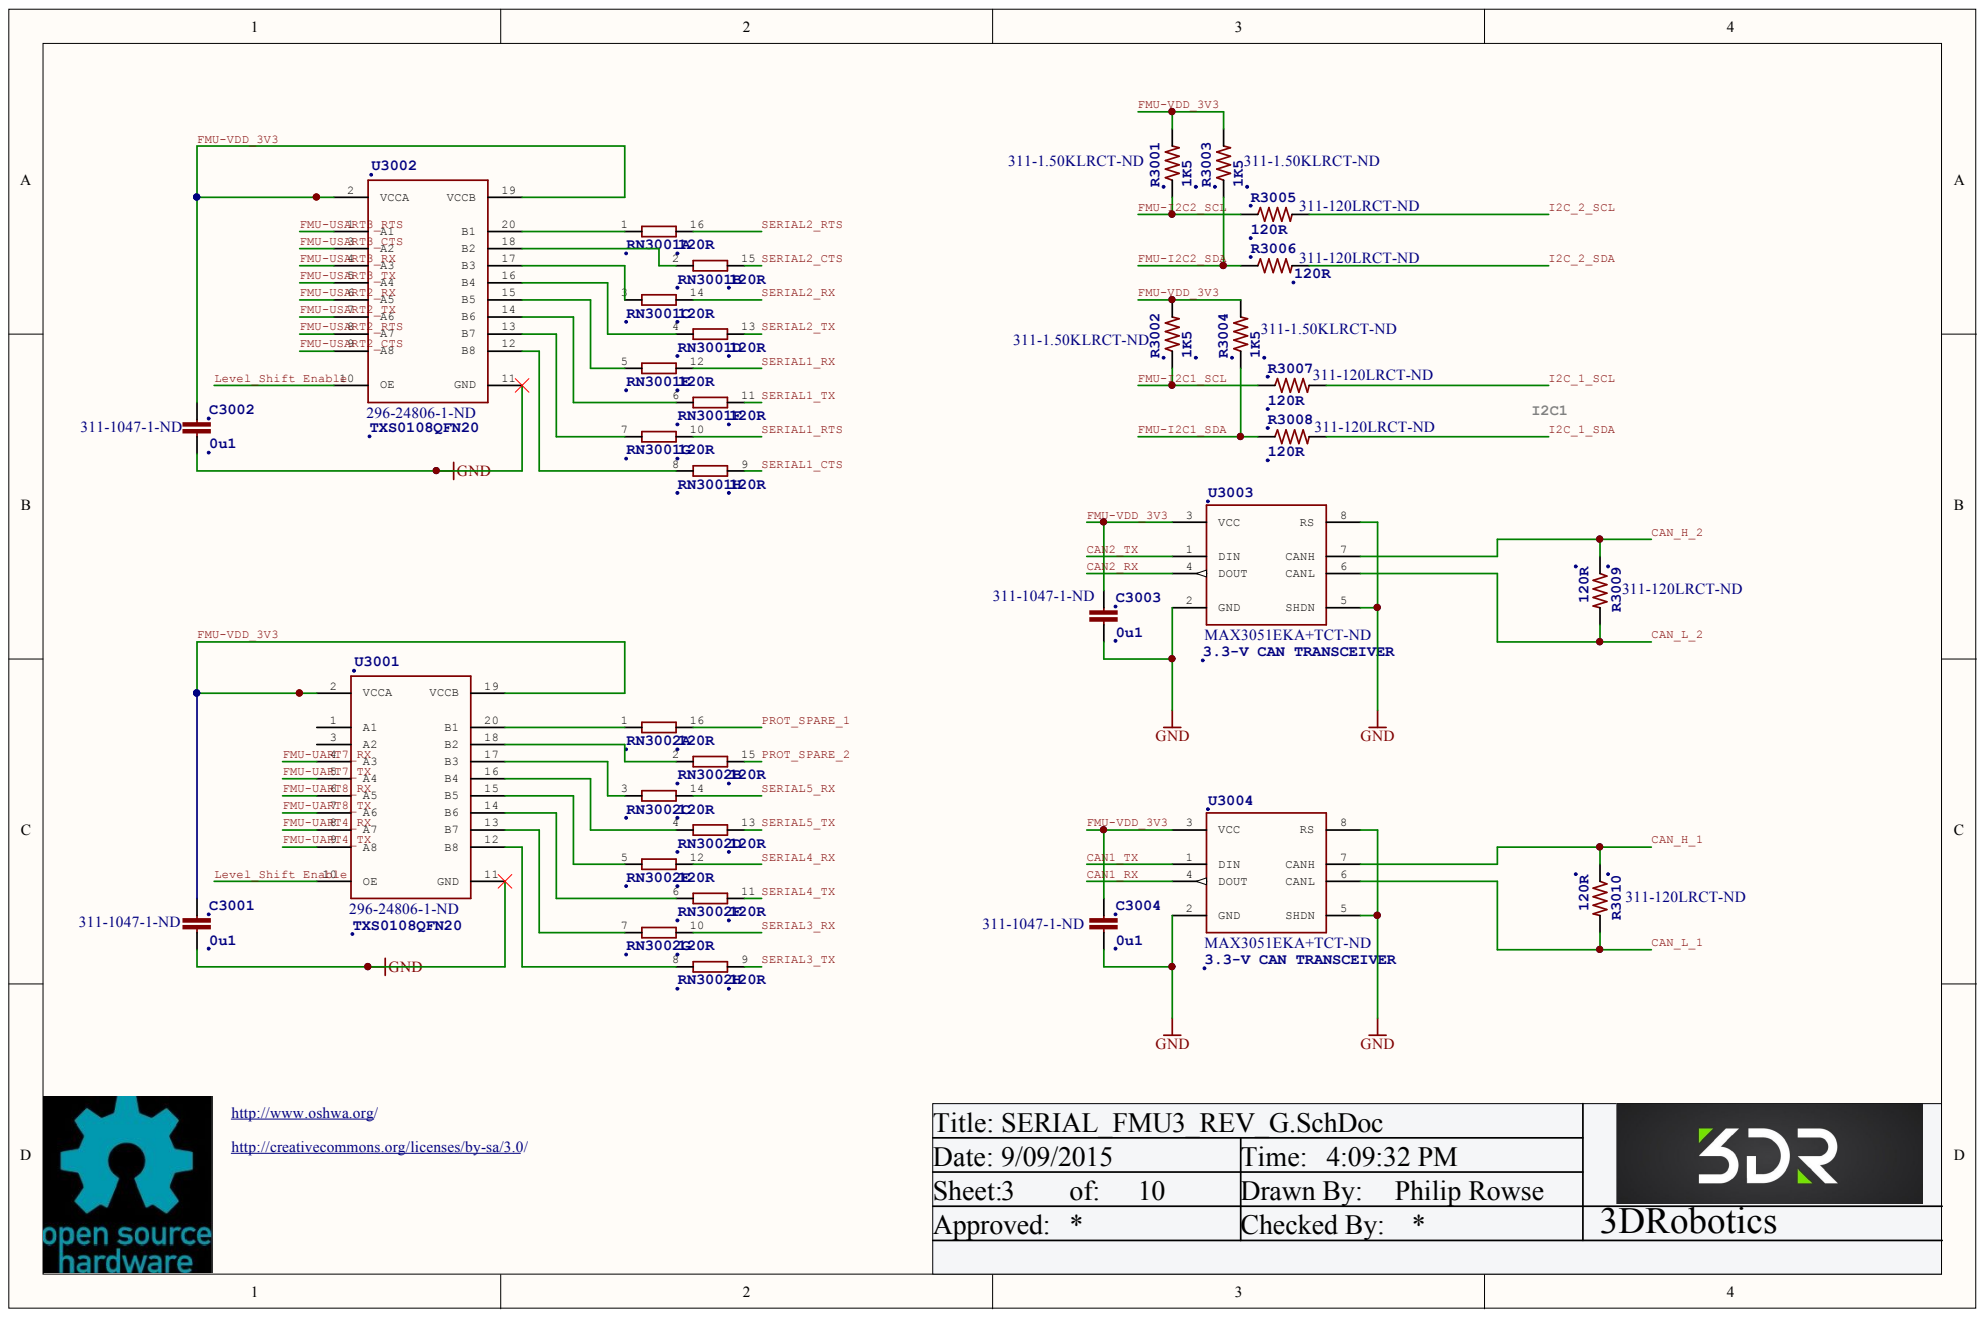
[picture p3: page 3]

Title: SERIAL_FMU3 _REV_G.SchDo c
Date: 9/0 9/2 0 1 5 | Time: 4:0 9:3 2 PM
Sheet: 3 of: 1 0 | Drawn By : Philip Rowse
Ap pro ved : * | Checked By : * | 3DRobotics

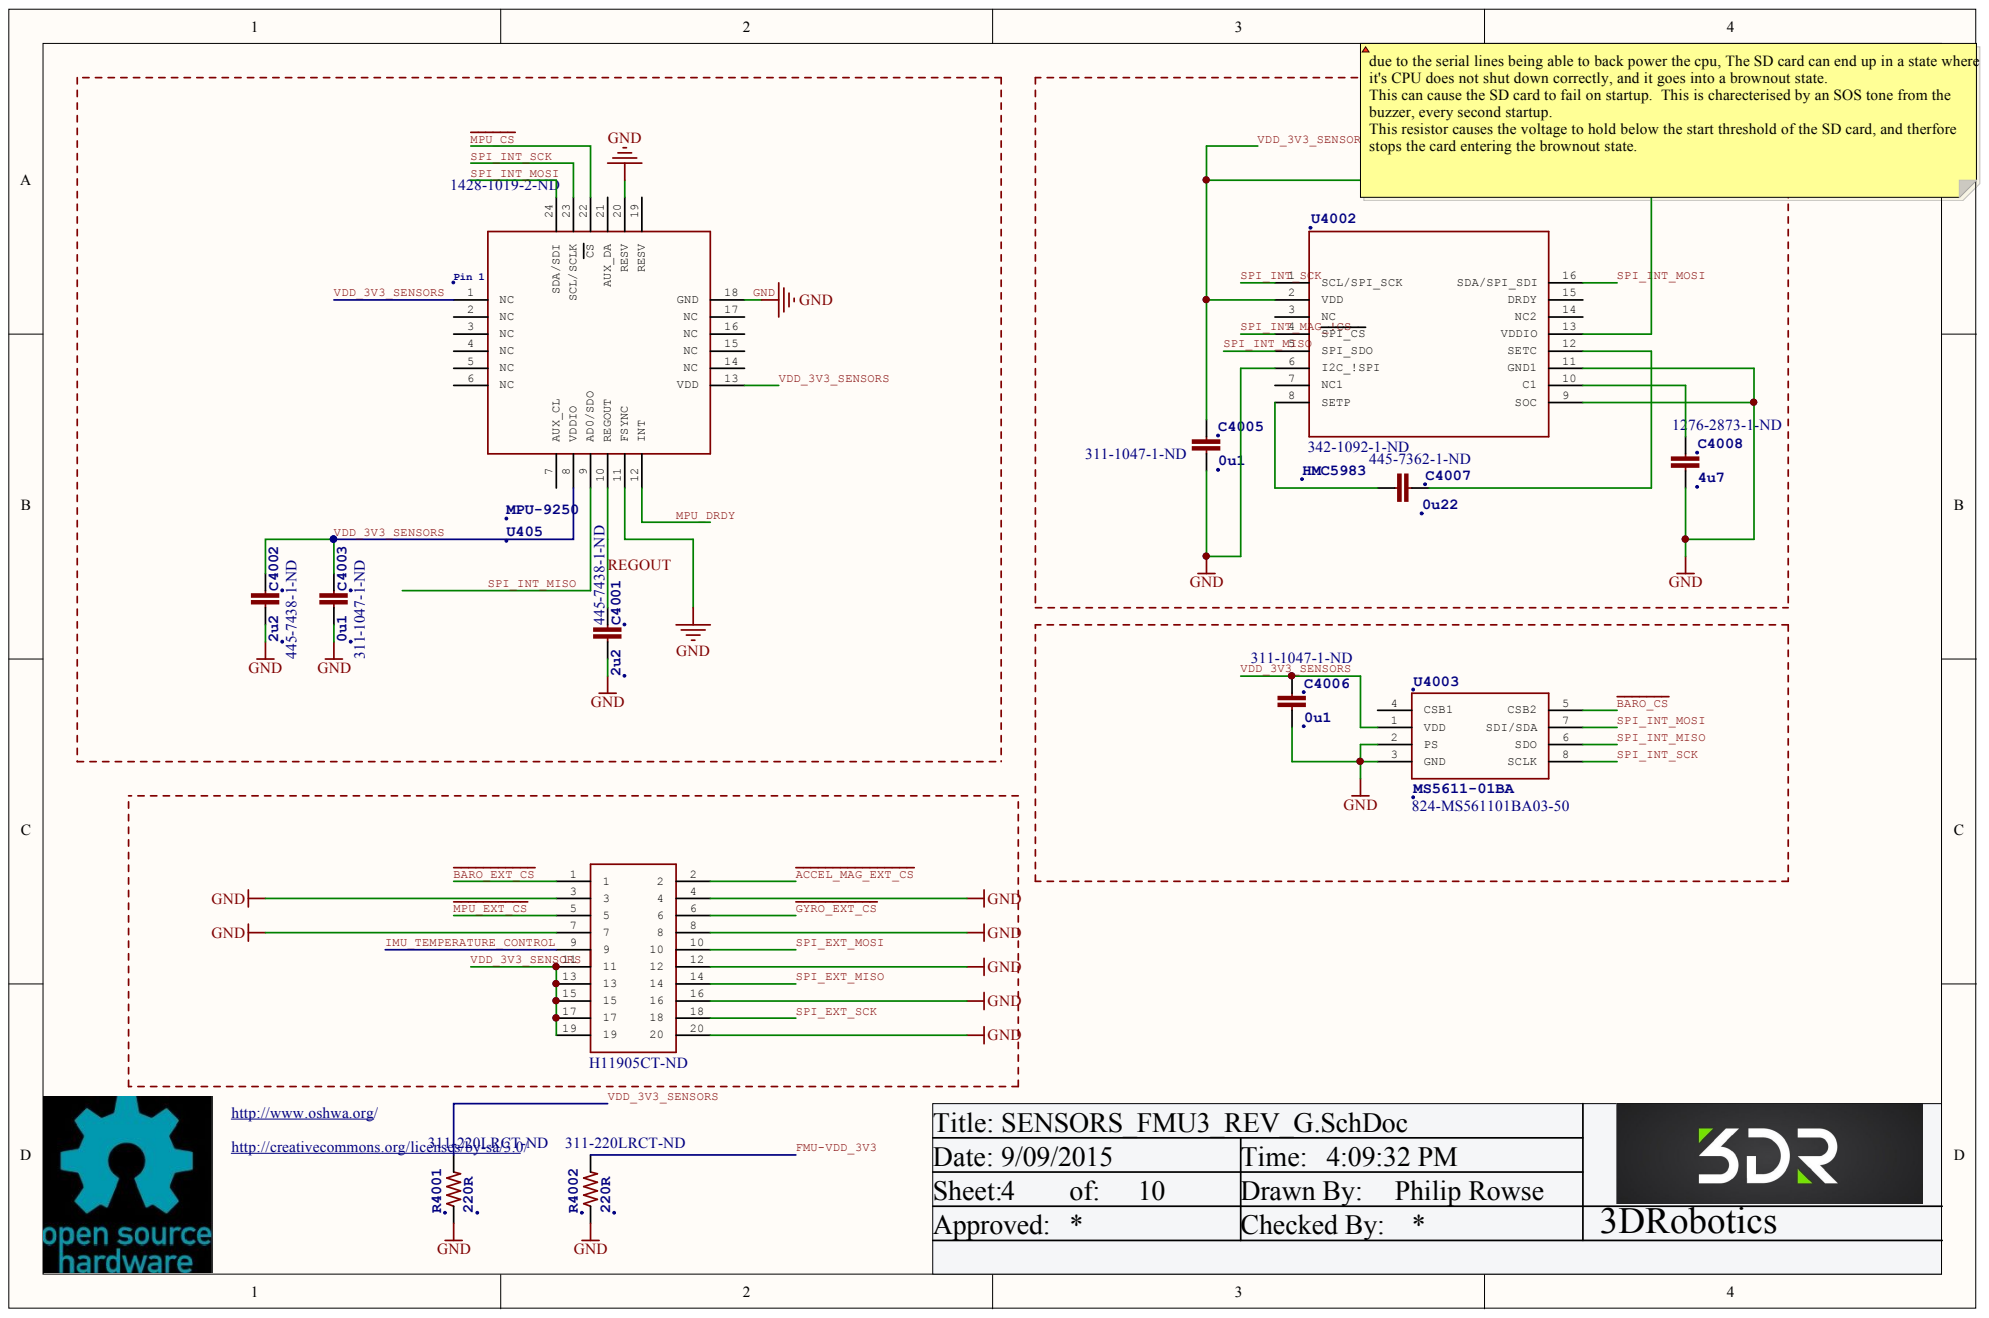
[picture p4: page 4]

he SD card, an

Date: 9/0 9/2 0 1 5 | Time: 4:0 9:3 2 PM
Sheet: 4 of: 1 0 | Drawn By : Philip Rowse
Ap pro ved : * | Checked By : * | 3DRobotics

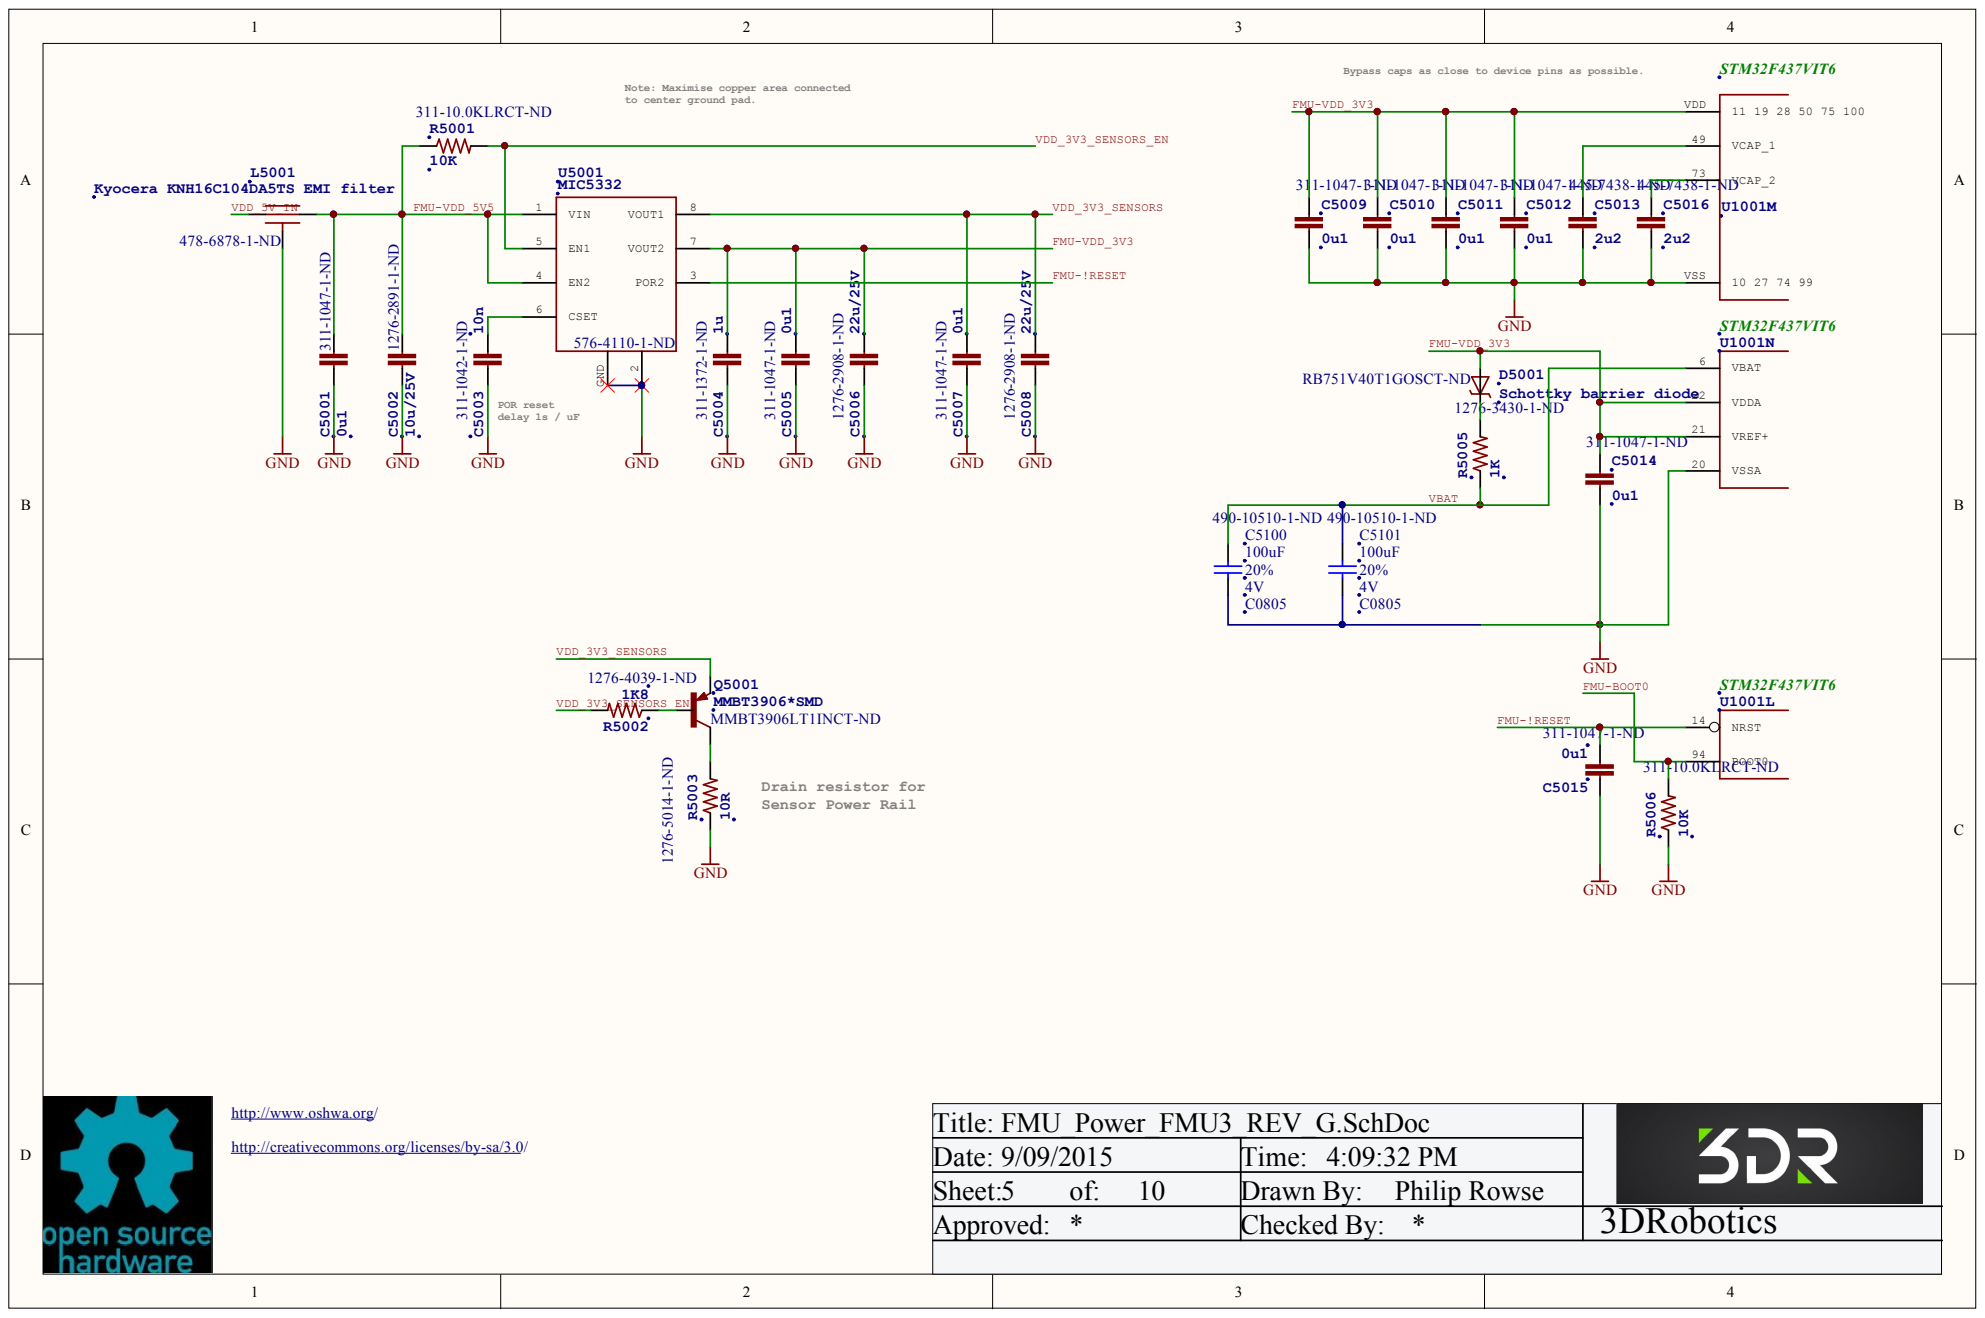
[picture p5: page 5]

Title: FMU_Power_FMU3 _REV_G.SchDo c
Date: 9/0 9/2 0 1 5 | Time: 4:0 9:3 2 PM
Sheet: 5 of: 1 0 | Drawn By : Philip Rowse
Ap pro ved : * | Checked By : * | 3DRobotics

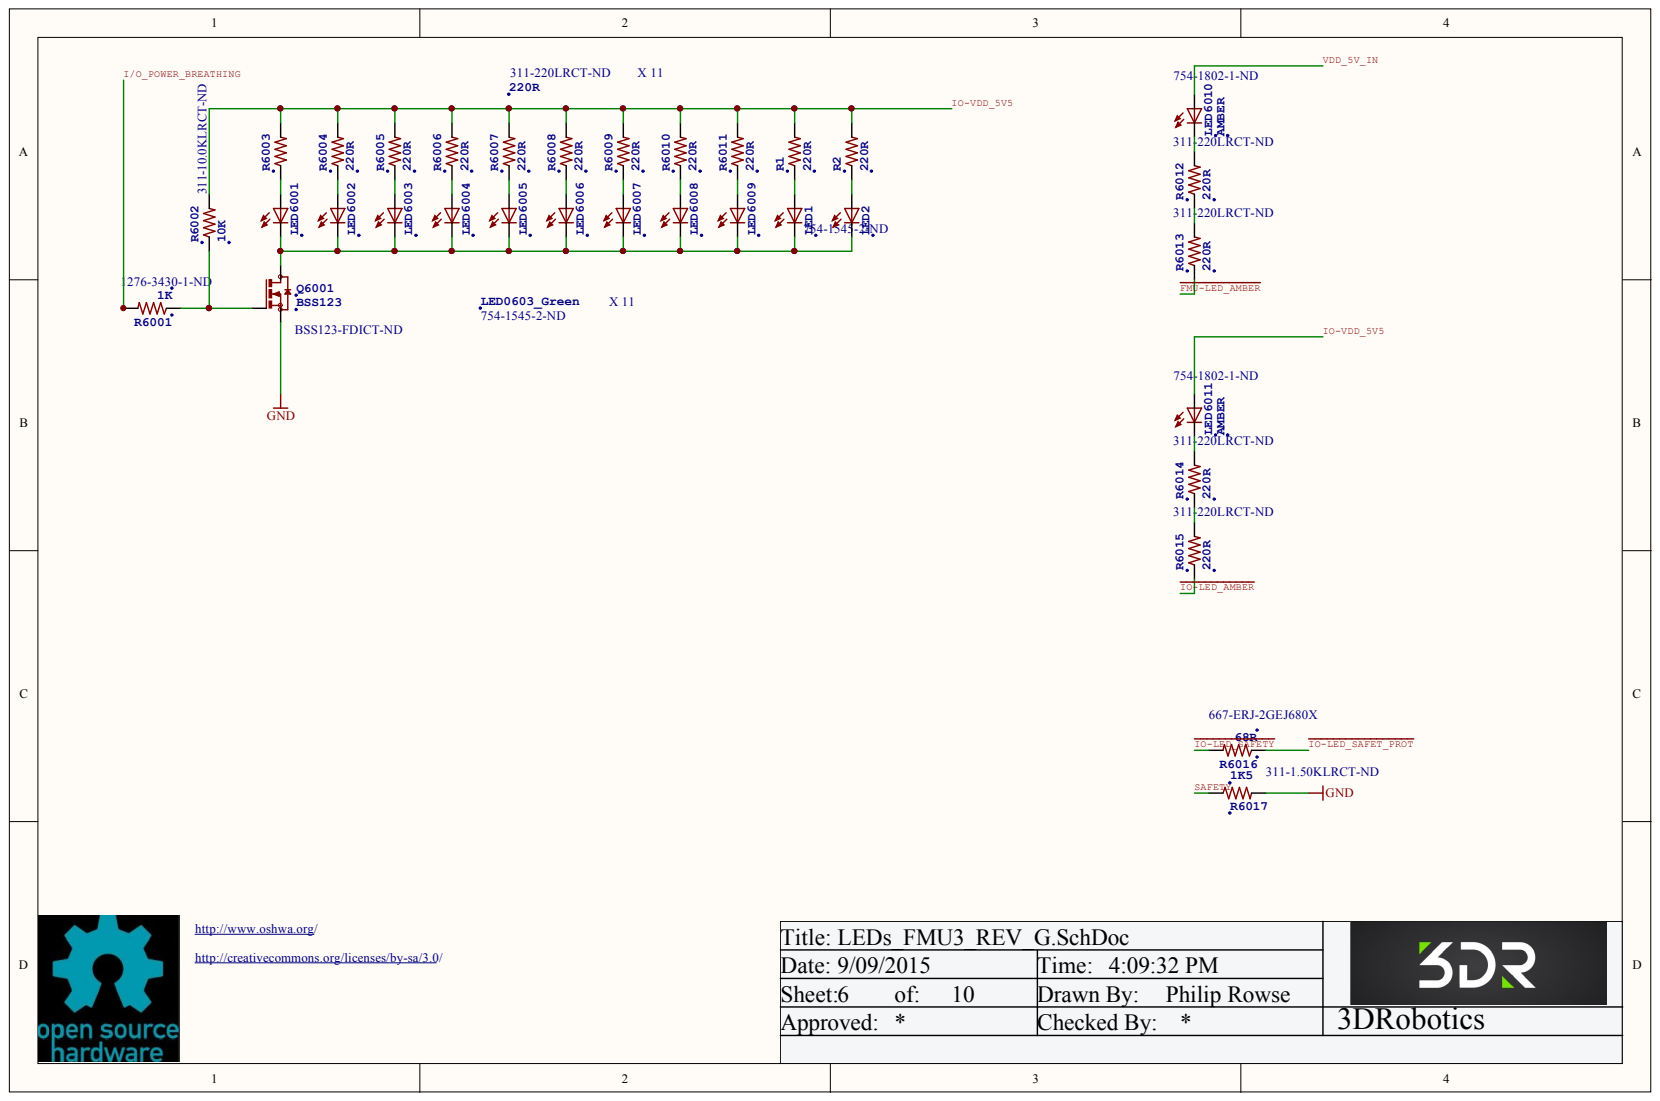
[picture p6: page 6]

Title: LEDs_FMU3 _REV_G.SchDo c
Date: 9/0 9/2 0 1 5 | Time: 4:0 9:3 2 PM
Sheet: 6 of: 1 0 | Drawn By : Philip Rowse
Ap pro ved : * | Checked By : * | 3DRobotics

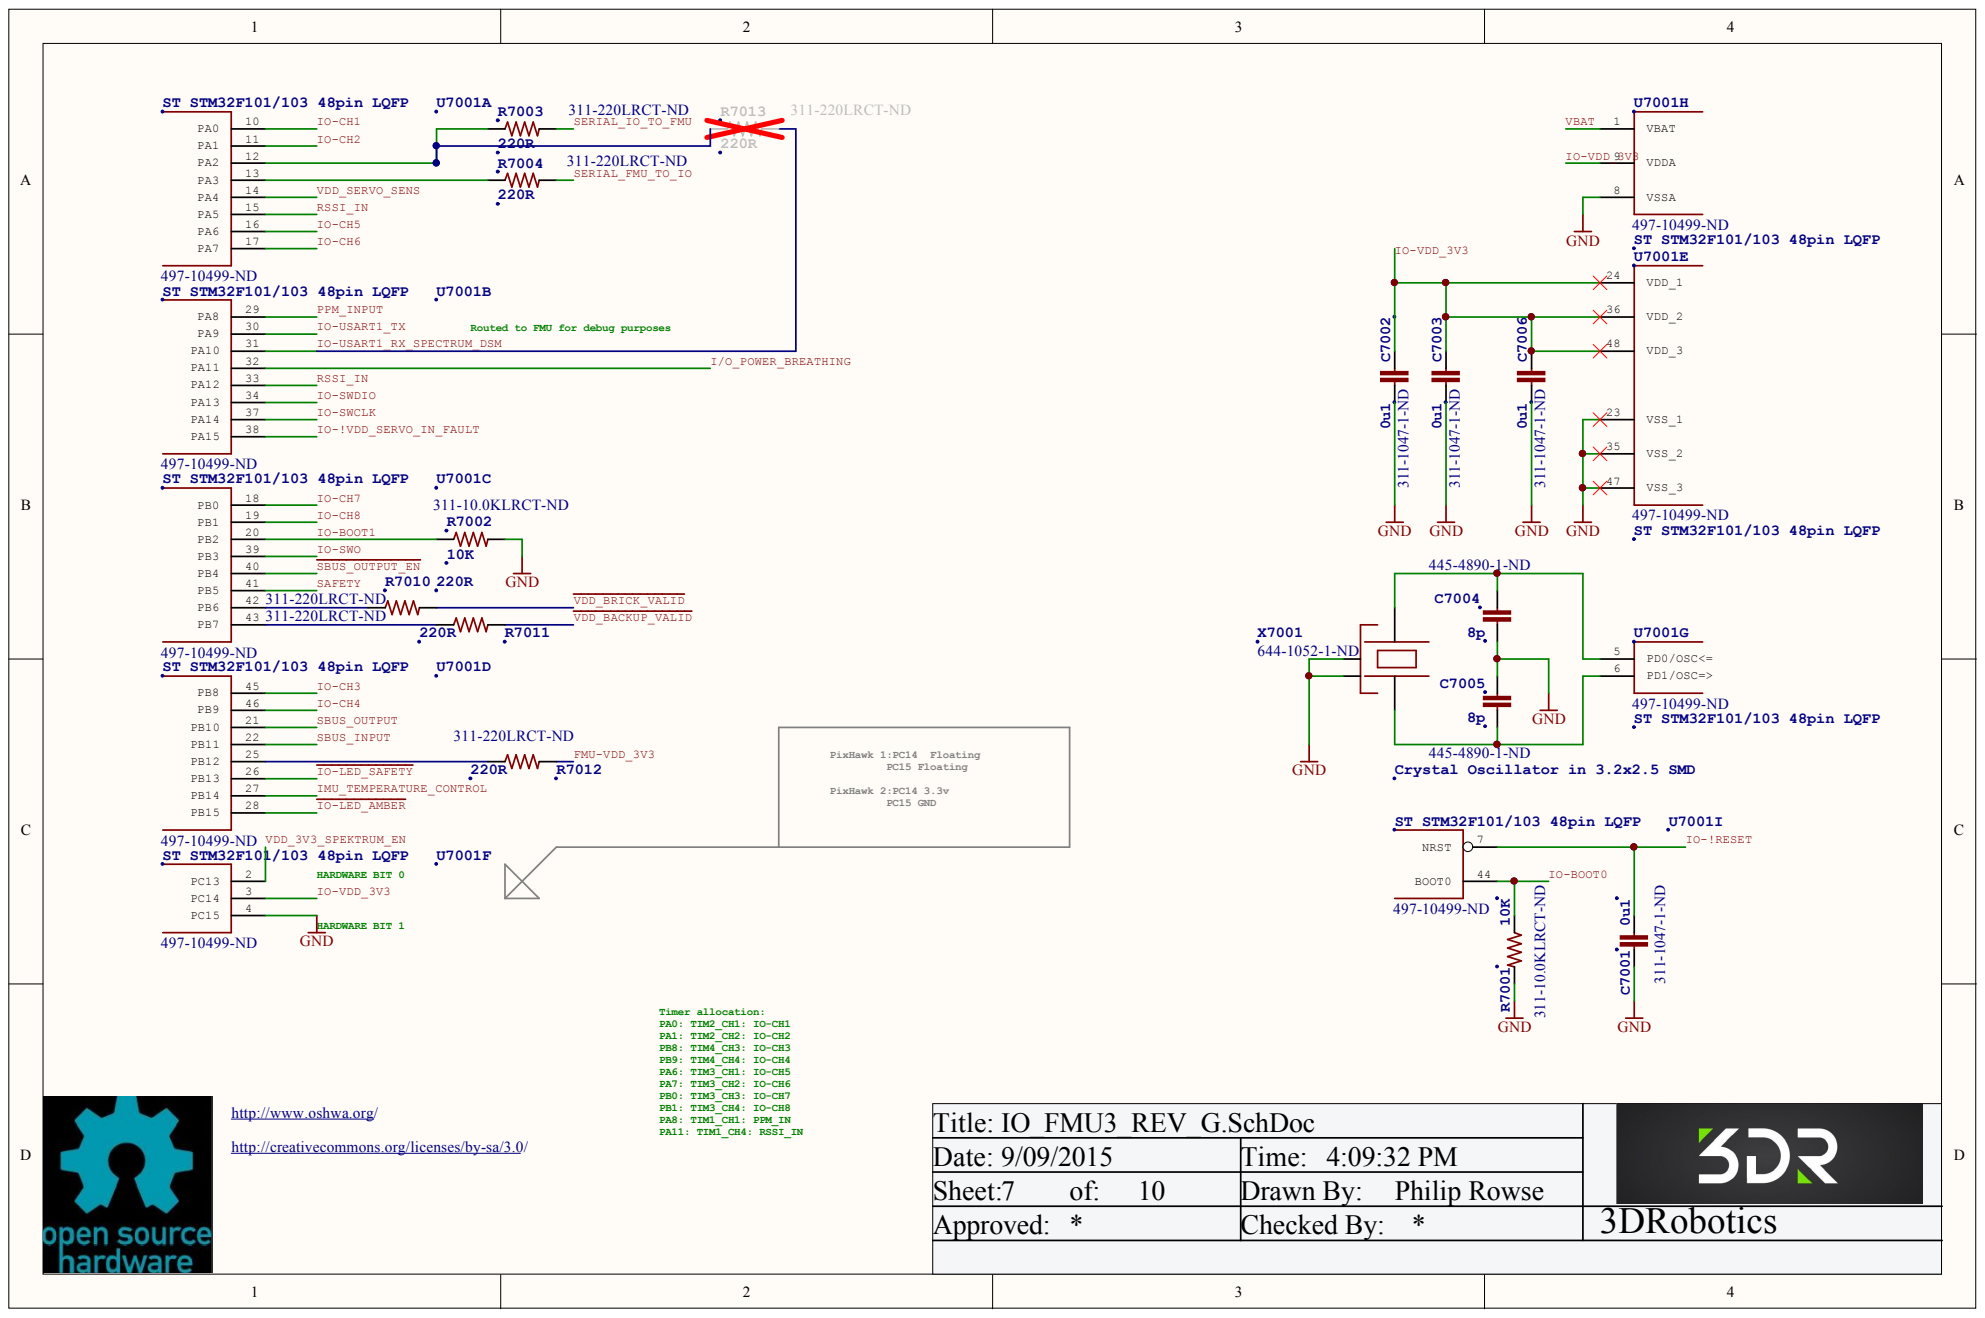
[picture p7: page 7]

1 1 | I O -C H 2 | 220R
1 2

Crystal Oscillator in 3.2x2.5 SMD 311-1047-1-ND C7006 0u1 311-1047-1-ND C7003 0u1 311-1047-1-ND

Title: IO_FMU3 _REV_G.SchDo c
Date: 9/0 9/2 0 1 5 | Time: 4:0 9:3 2 PM
Sheet: 7 of: 1 0 | Drawn By : Philip Rowse
Ap pro ved : * | Checked By : * | 3DRobotics

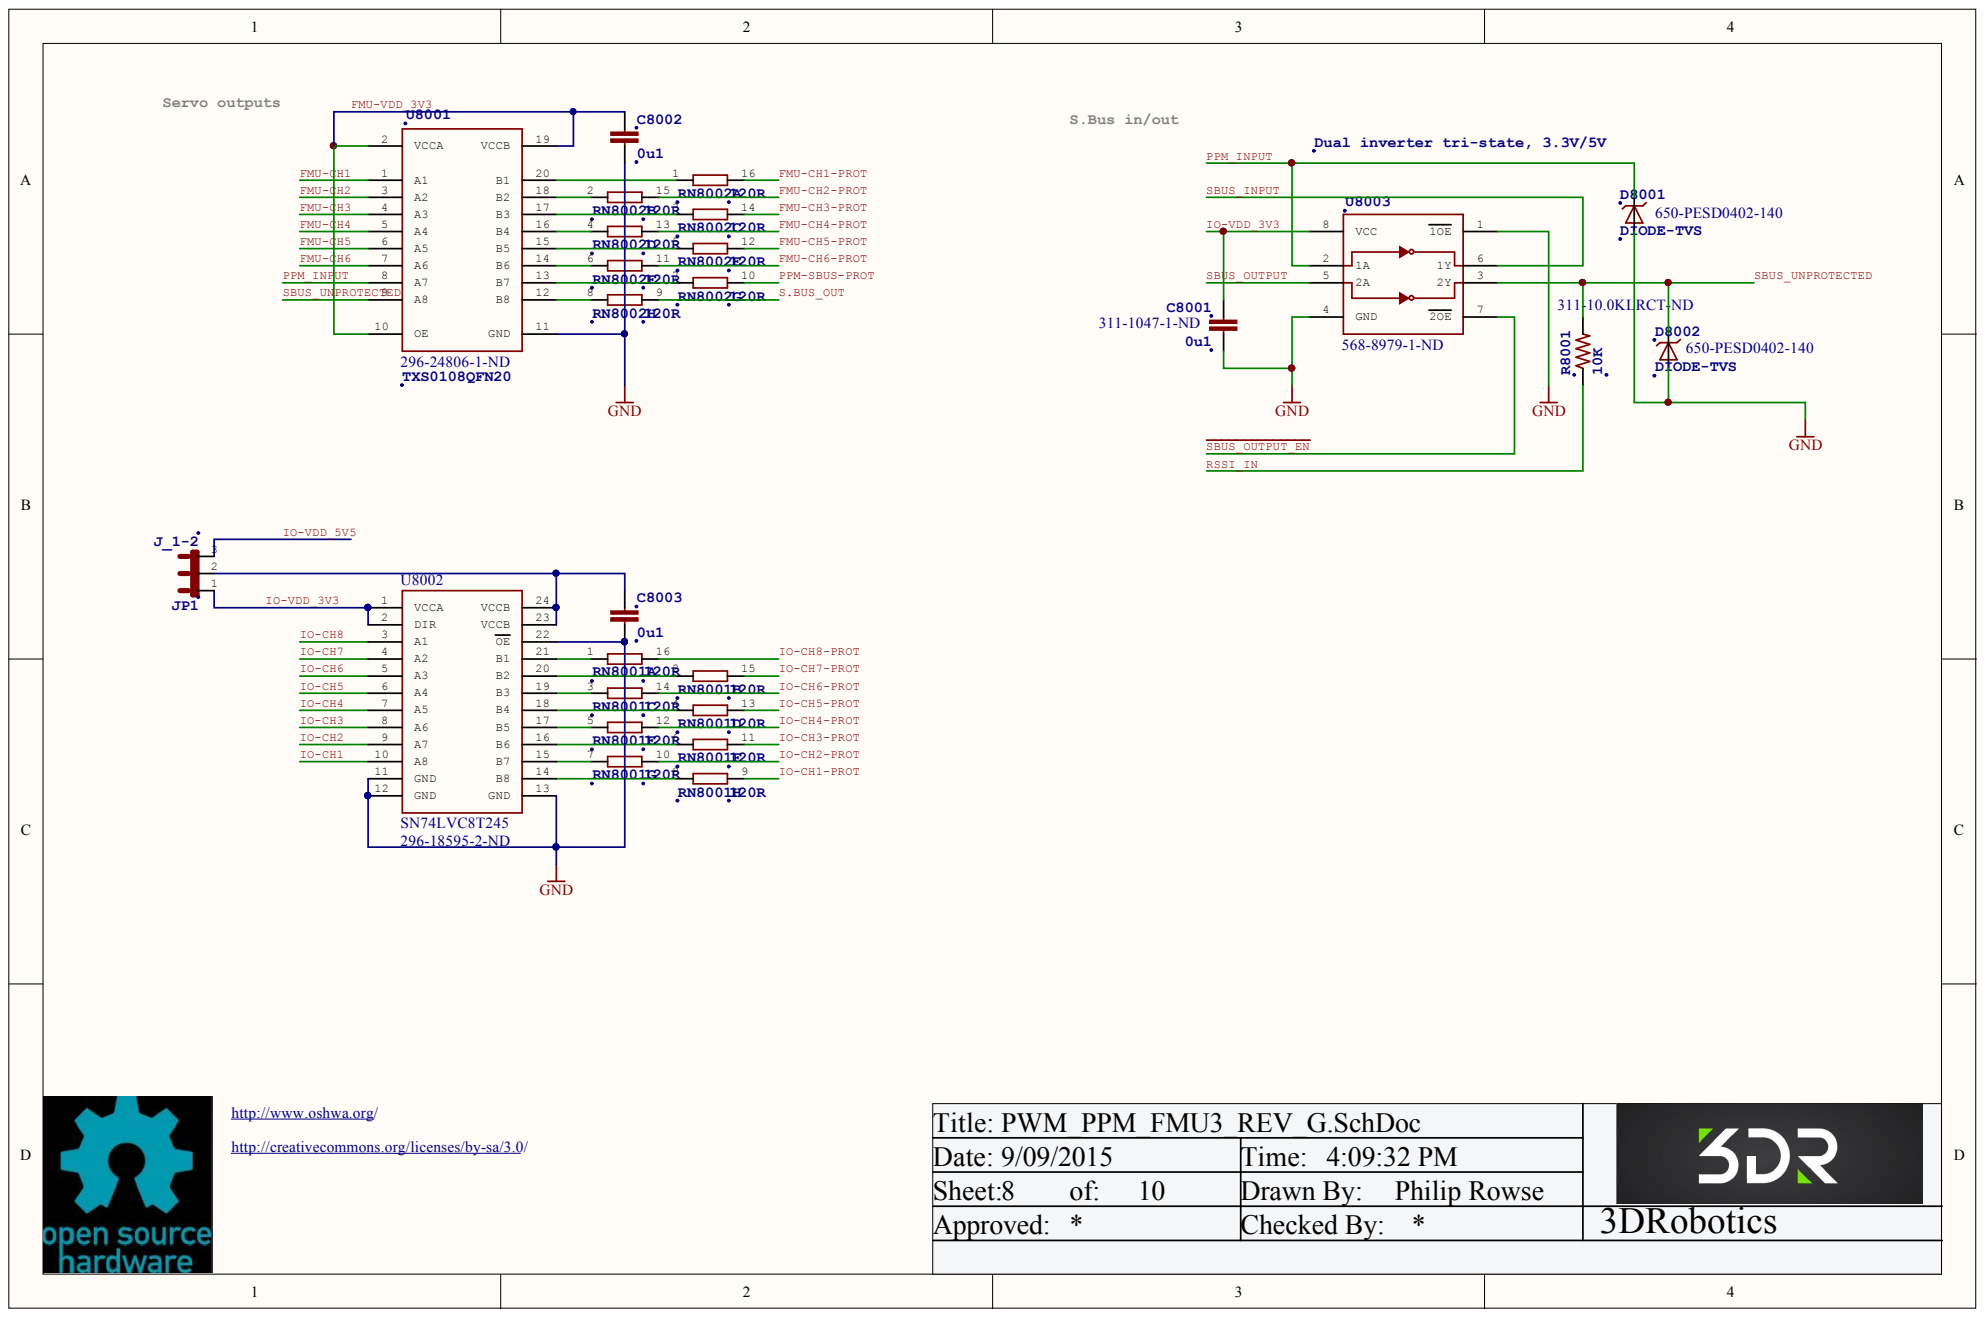
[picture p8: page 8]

Dual inverter tri-state, 3.3V/5V 311-10.0

1 7
1 6 | RN8001E120R6
1 5

Title: PWM _PPM _FMU3 _REV_G.SchDo c
Date: 9/0 9/2 0 1 5 | Time: 4:0 9:3 2 PM
Sheet: 8 of: 1 0 | Drawn By : Philip Rowse
Ap pro ved : * | Checked By : * | 3DRobotics

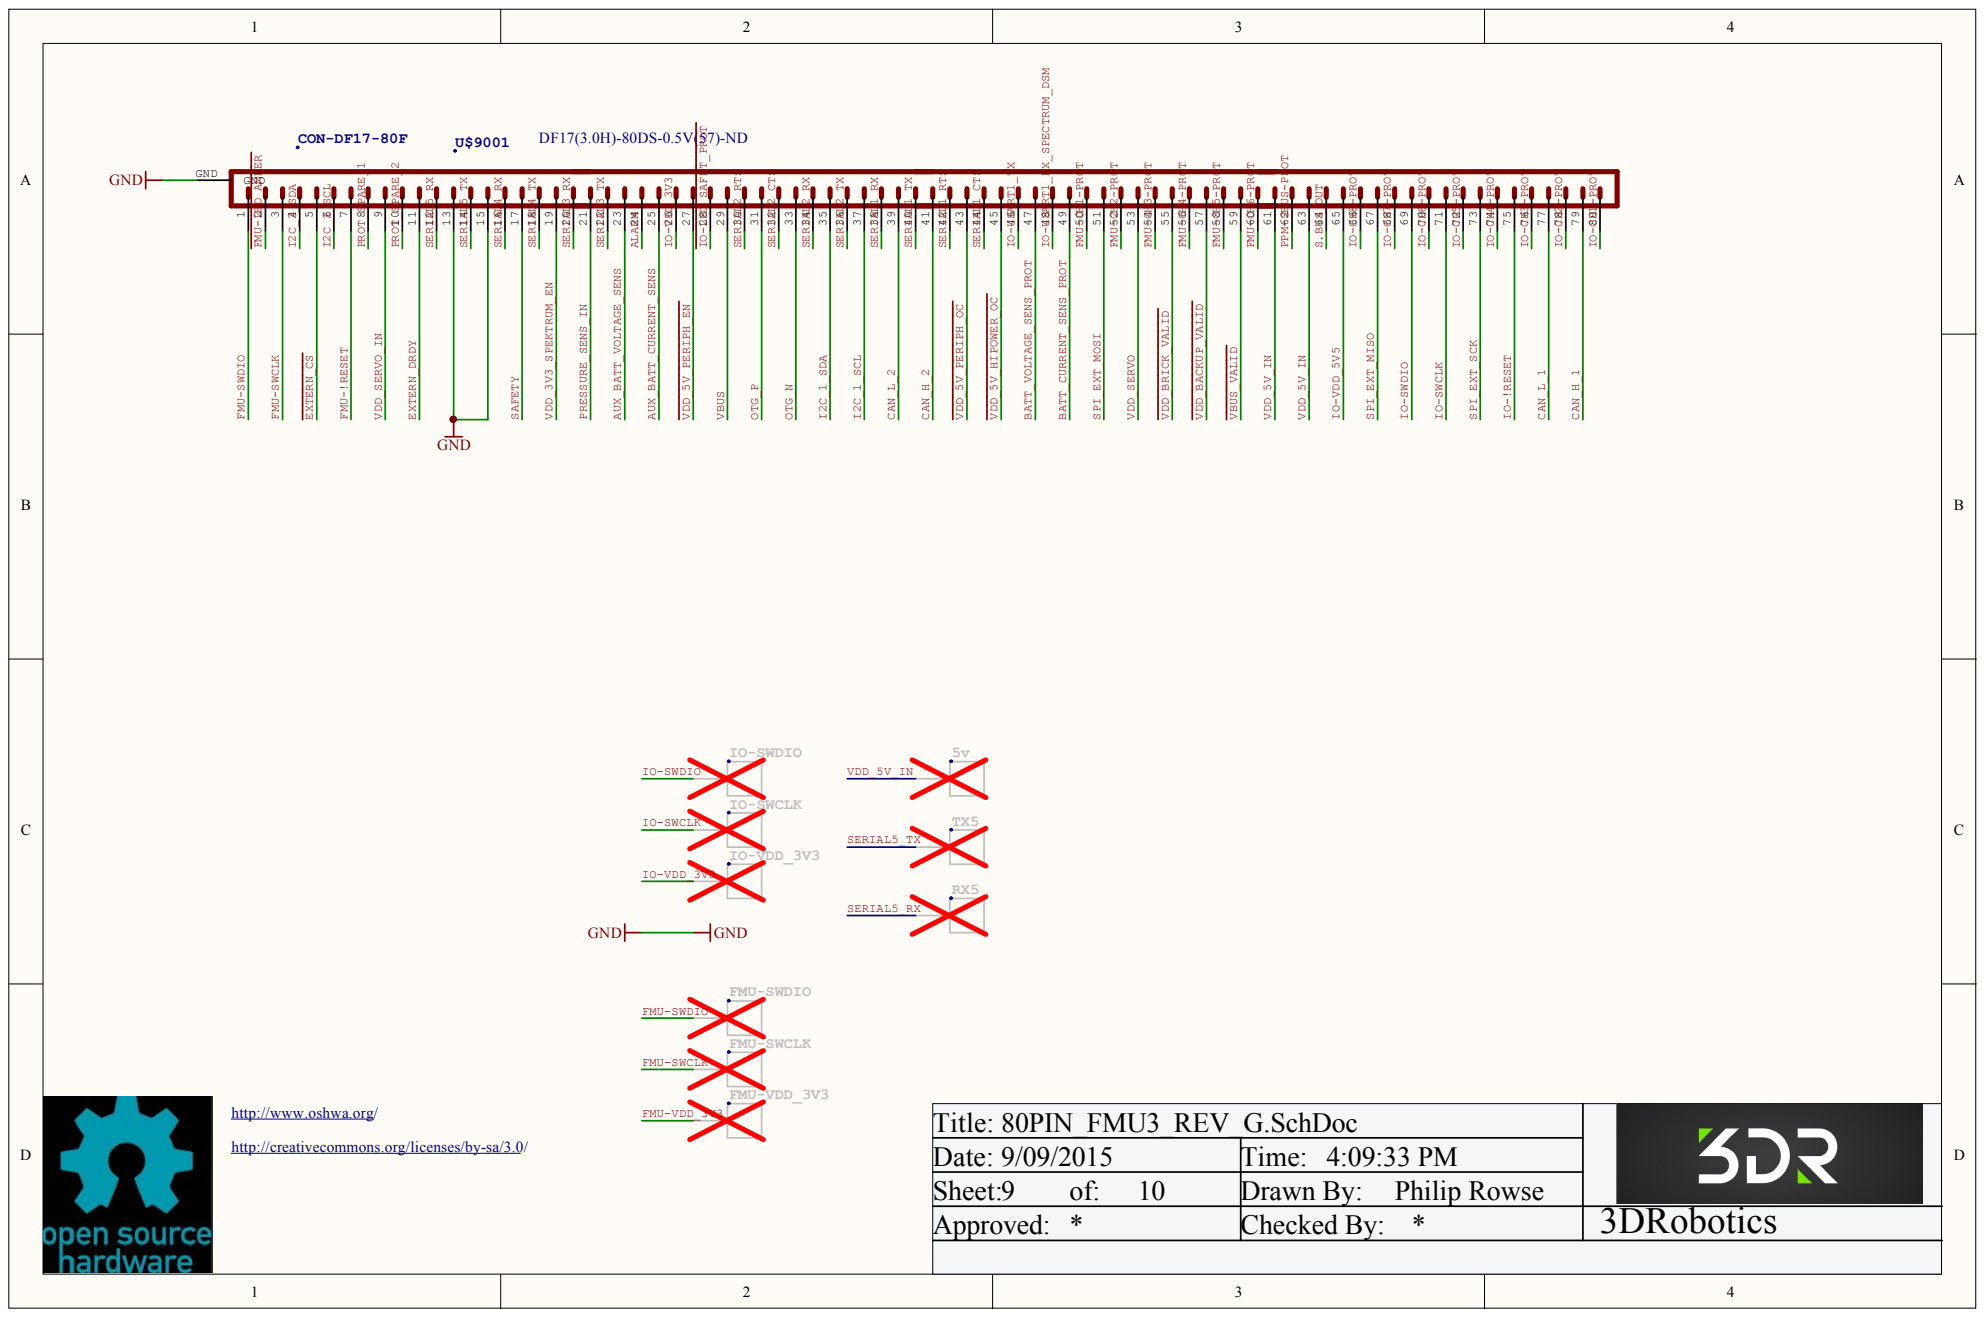
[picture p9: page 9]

http://www.oshwa.org/

Title: 80PIN_FMU3_REV_G.SchDoc
Date: 9/09/2015 | Time: 4:09:33 PM
Sheet:9 of: 10 | Drawn By: Philip Rowse
Approved: * | Checked By: * | 3DRobotics

http://creativecommons.org/licenses/by-sa/3.0/

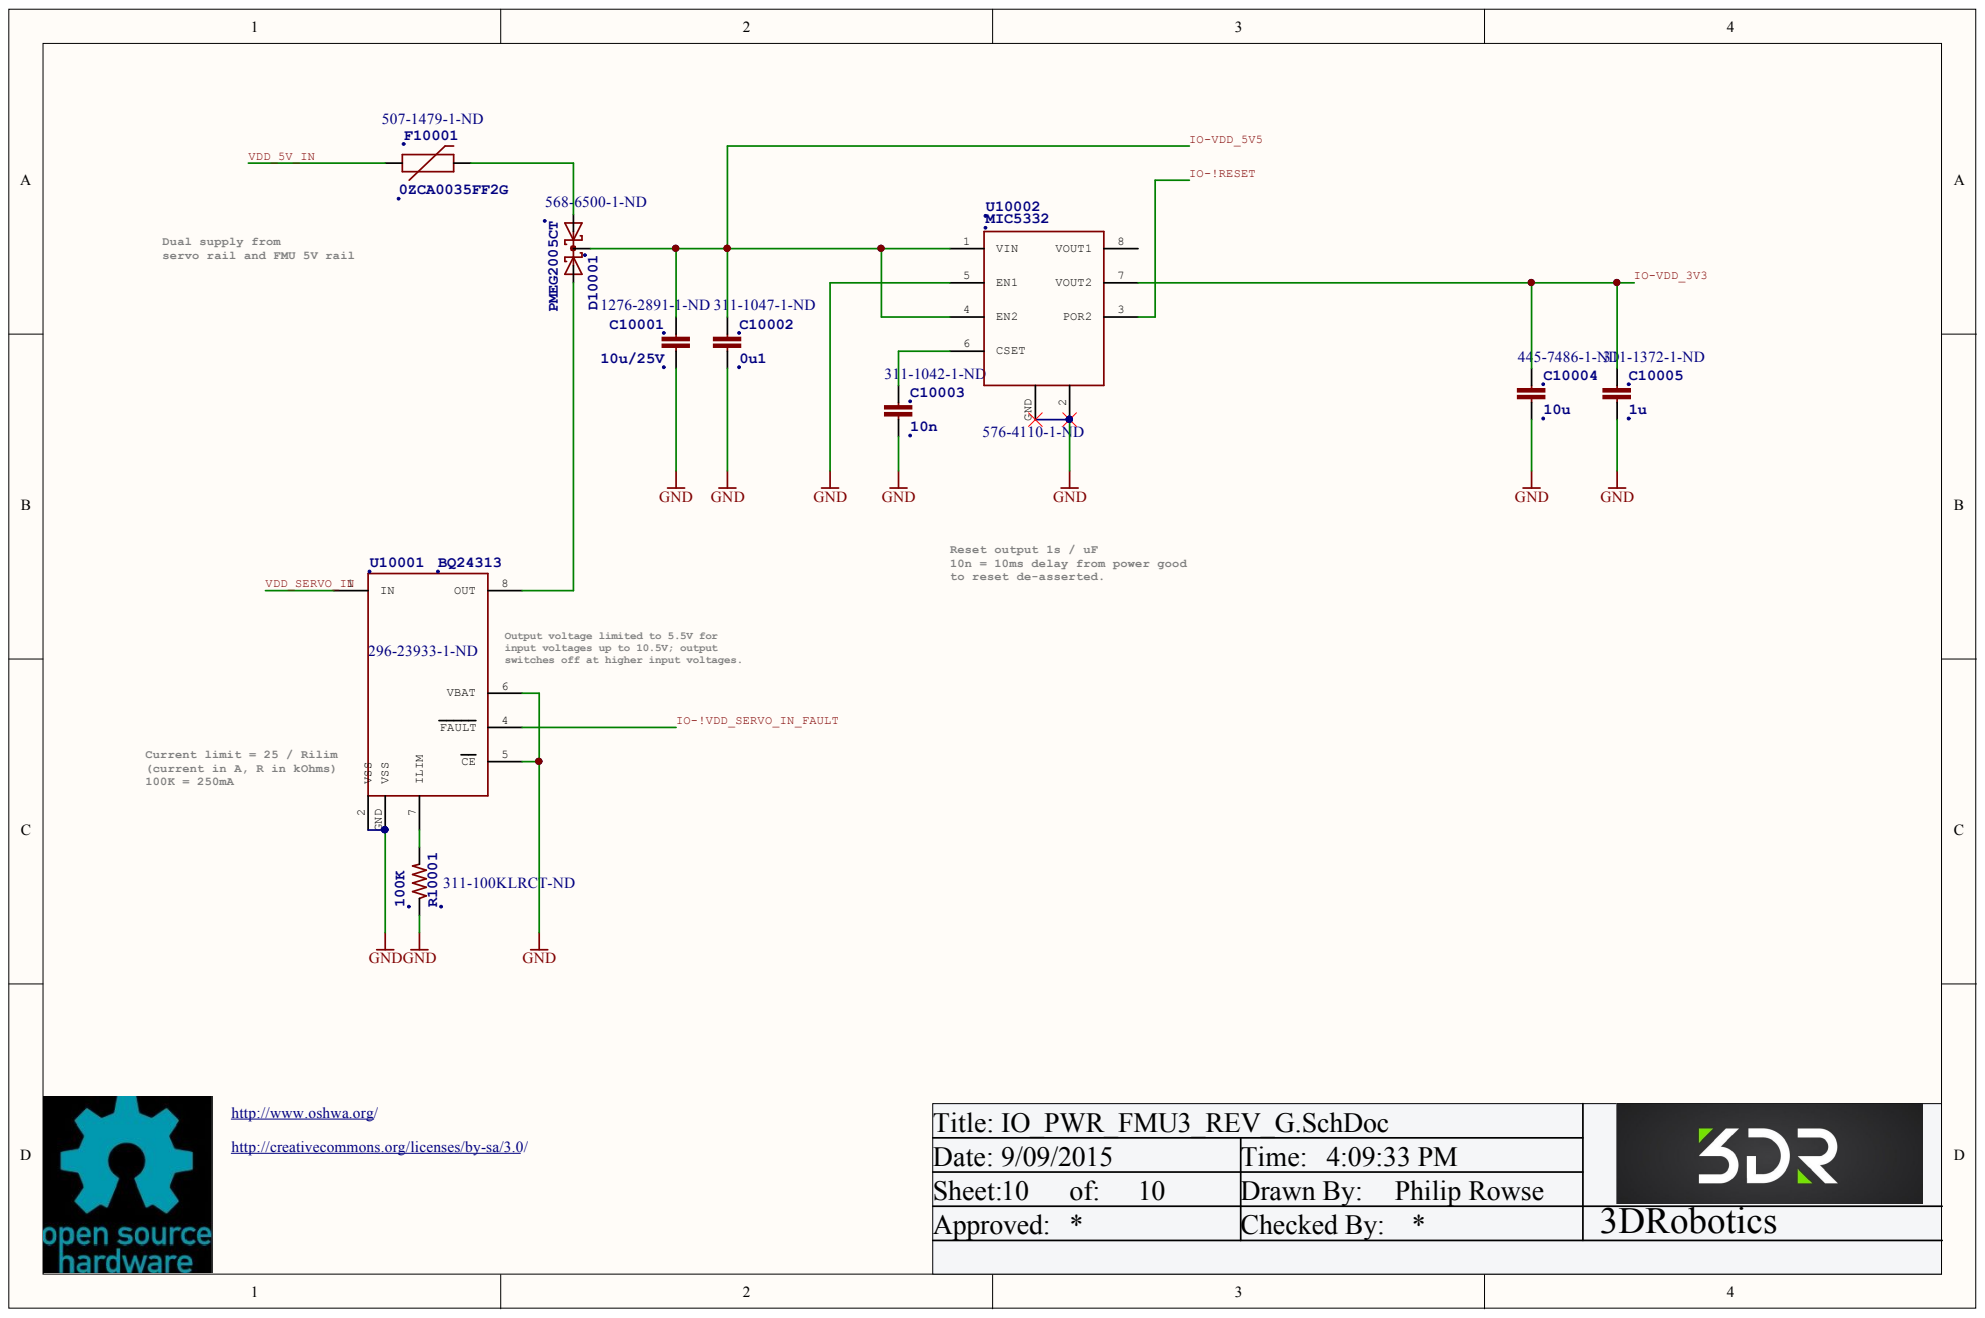
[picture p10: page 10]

Dual supply from
servo rail and FMU 5V rail

Reset output 1s / uF
10n = 10ms delay from power good
to reset de-asserted.

Output voltage limited to 5.5V for
input voltages up to 10.5V; output
switches off at higher input voltages.

Current limit = 25 / Rilim
(current in A, R in kOhms)

http://www.oshwa.org/

Title: IO_PWR_FMU3_REV_G.SchDoc
Date: 9/09/2015 | Time: 4:09:33 PM
Sheet:10 of: 10 | Drawn By: Philip Rowse
Approved: * | Checked By: * | 3DRobotics

http://creativecommons.org/licenses/by-sa/3.0/

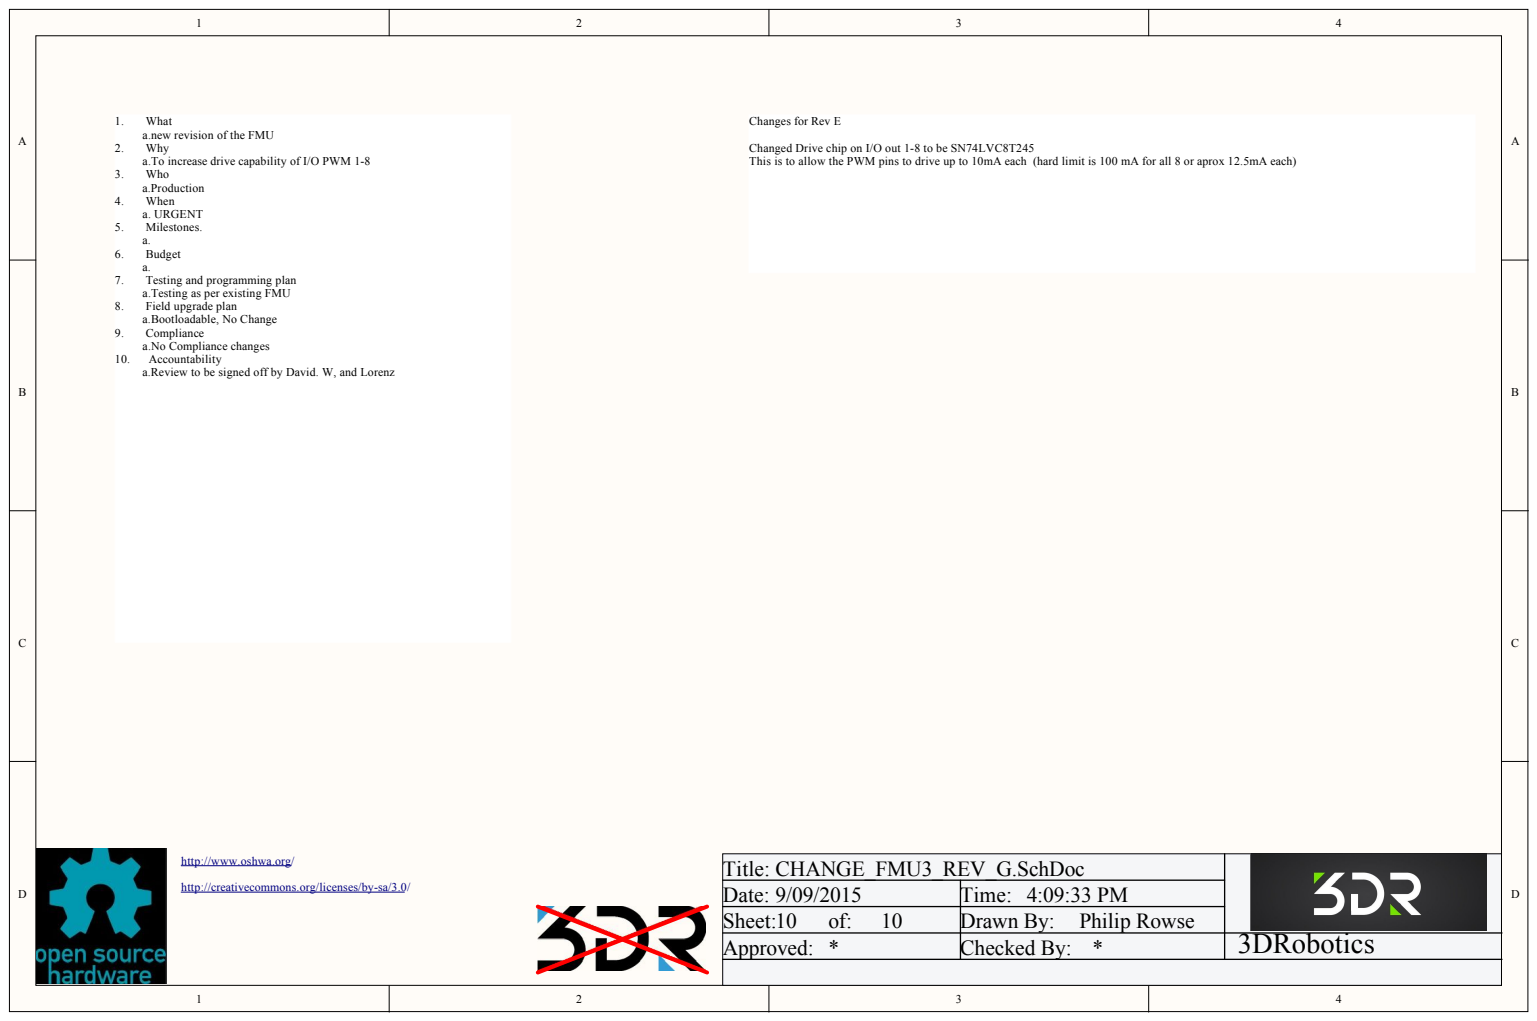
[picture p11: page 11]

1. What
a.new revision of the FMU
2. Why
a.To increase drive capability of I/O PWM 1-8
3. Who
a.Production
4. When
a. URGENT
5. Milestones.
6. Budget
7. Testing and programming plan
a.Testing as per existing FMU
8. Field upgrade plan
a.Bootloadable, No Change
9. Compliance
a.No Compliance changes
10. Accountability
a.Review to be signed off by David. W, and Lorenz

Changed Drive chip on I/O out 1-8 to be SN74LVC8T245
This is to allow the PWM pins to drive up to 10mA each (hard limit is 100 mA for all 8 or aprox 12.5mA each)

http://www.oshwa.org/

Title: CHANGE_FMU3_REV_G.SchDoc
Date: 9/09/2015 | Time: 4:09:33 PM
Sheet:10 of: 10 | Drawn By: Philip Rowse
Approved: * | Checked By: * | 3DRobotics

http://creativecommons.org/licenses/by-sa/3.0/

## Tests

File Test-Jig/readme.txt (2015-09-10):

this folder contains pictures of the jig setup without the covers on.
It contains all schematics, BOMs, Gerbers, required to build this.

This also contains all Firmware needed to program the JTAG, and PWM parts of the board.

The actual linux files are in Git.

in the folder called test jig master, there is an overall schematic.

Test Jig hardware contains all the hardware needed to build the system

Feel free to add any notes to this folder for future reference

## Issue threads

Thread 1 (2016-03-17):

Eagle files?

steveheinsch, 2016-03-17:
I don't have Altium designer or anything else that will convert these files to Eagle, or other freeware program. Is it possible to provide them in additional formats?

proficnc, 2016-03-17:
No, these files were all done originally in Altium. Eagle is not free either....

The full schematics and Gerbers are supplied.

Also, these drawings are out of date.

Pixhawk2 will be on sale starting from June to the general public, up to date drawings will be released when these hit the market.

Any questions, feel free to join the conversation at the Pixhawk 2 Facebook page, or Twitter etc, or jump on drones discuss Google groups.

If your a manufacturer that wishes to support the project, feel free to contact me, and I will be happy to work with you if your willing to support the project.

Closed 2017-02-20.

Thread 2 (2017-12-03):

PCA_0005_FULL_CB_REV_A.SCHLIB Library is missing

samiahmari, 2017-12-03:
This is a main library for Carrier board which nit included in repository. Wondering if it  is possible to add this to repository.

proficnc, 2017-12-03:
This repository is out of date.
And no, I don’t release my library.
In altium, you don’t need to, you simply export it from the file.

Updated correct drawings are in the ProfiCNC git

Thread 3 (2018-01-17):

IO-VDD_5V5

zouboan, 2018-01-17:
The schematic and PCB file published on GitHub shows the IO-VDD_5V5  in 80pin is the same signal as the IO-VDD_5V5  in FMU-V3,But when I measured it with a multimeter, I found that there was an impedance of 25k ohms between the two,and the actual voltage of IO-VDD_5V5  in the 80pin connector is 1.7V,why?

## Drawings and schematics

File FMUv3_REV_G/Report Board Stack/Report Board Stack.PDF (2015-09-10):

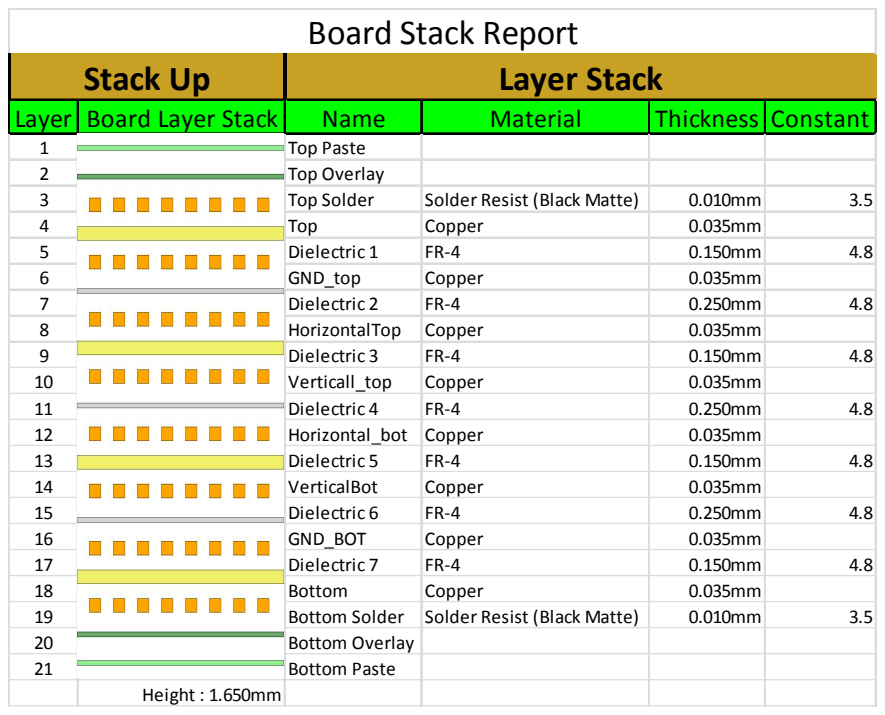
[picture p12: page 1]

Stack Up | Layer Stack
Layer | Board Layer Stack | Name | Material | Thickness | Constant
1 | | Top Paste
2 | | Top Overlay
3 | | Top Solder | Solder Resist (Black Matte) | 0.010mm | 3.5
4 | | Top | Copper | 0.035mm
5 | | Dielectric 1 | FR-4 | 0.150mm | 4.8
6 | | GND_top | Copper | 0.035mm
7 | | Dielectric 2 | FR-4 | 0.250mm | 4.8
8 | | HorizontalTop | Copper | 0.035mm
9 | | Dielectric 3 | FR-4 | 0.150mm | 4.8
10 | | Verticall_top | Copper | 0.035mm
11 | | Dielectric 4 | FR-4 | 0.250mm | 4.8
12 | | Horizontal_bot | Copper | 0.035mm
13 | | Dielectric 5 | FR-4 | 0.150mm | 4.8
14 | | VerticalBot | Copper | 0.035mm
15 | | Dielectric 6 | FR-4 | 0.250mm | 4.8
16 | | GND_BOT | Copper | 0.035mm
17 | | Dielectric 7 | FR-4 | 0.150mm | 4.8
18 | | Bottom | Copper | 0.035mm
19 | | Bottom Solder | Solder Resist (Black Matte) | 0.010mm | 3.5
20 | | Bottom Overlay
21 | | Bottom Paste

Height : 1.650mm

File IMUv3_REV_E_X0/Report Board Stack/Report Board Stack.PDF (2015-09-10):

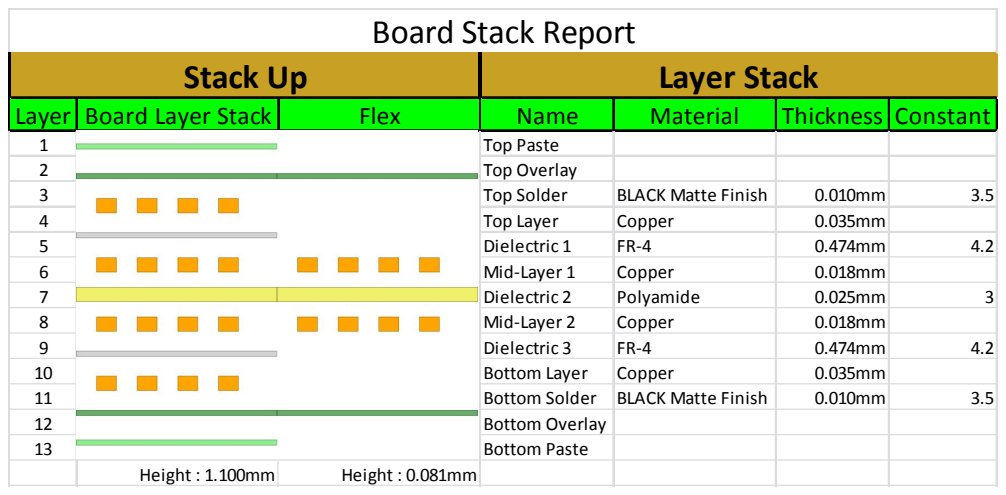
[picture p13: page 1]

Stack Up | Layer Stack

Layer | Board Layer Stack | Flex | Name | Material | Thickness | Constant
1 | | | Top Paste
2 | | | Top Overlay
3 | | | Top Solder | BLACK Matte Finish | 0.010mm | 3.5
4 | | | Top Layer | Copper | 0.035mm
5 | | | Dielectric 1 | FR-4 | 0.474mm | 4.2
6 | | | Mid-Layer 1 | Copper | 0.018mm
7 | | | Dielectric 2 | Polyamide | 0.025mm | 3
8 | | | Mid-Layer 2 | Copper | 0.018mm
9 | | | Dielectric 3 | FR-4 | 0.474mm | 4.2
10 | | | Bottom Layer | Copper | 0.035mm
11 | | | Bottom Solder | BLACK Matte Finish | 0.010mm | 3.5
12 | | | Bottom Overlay
13 | | | Bottom Paste

Height : 1.100mm | Height : 0.081mm

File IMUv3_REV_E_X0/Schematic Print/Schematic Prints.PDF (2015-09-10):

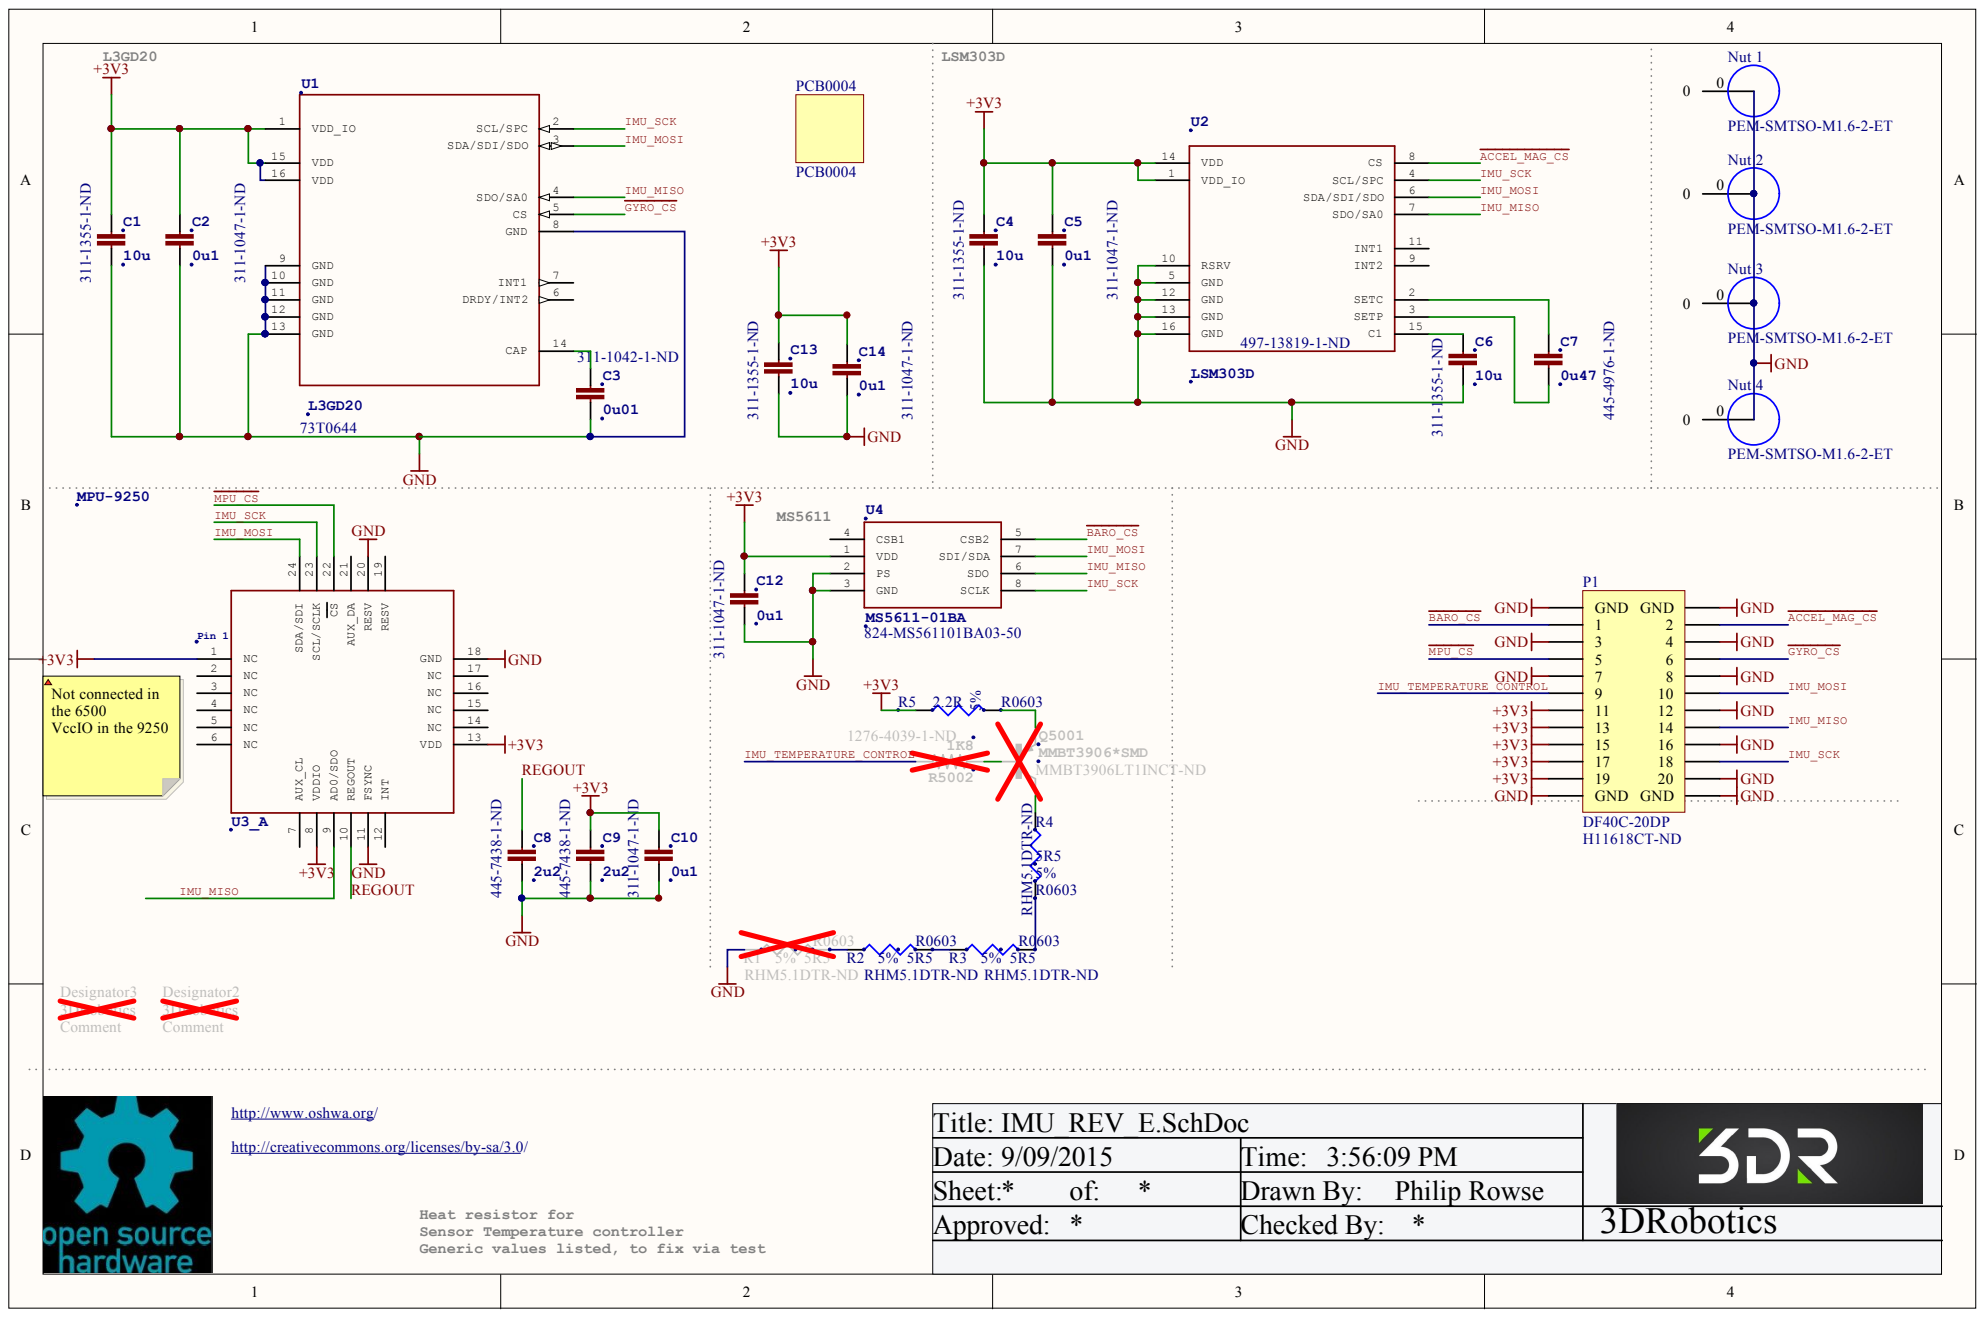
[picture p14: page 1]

SCL/SCLK 23 SDA/SDI 24

http://www.oshwa.org/

Title: IMU_REV_E.SchDoc
Date: 9/09/2015 | Time: 3:56:09 PM
Sheet:* of: * | Drawn By: Philip Rowse
Approved: * | Checked By: * | 3DRobotics

http://creativecommons.org/licenses/by-sa/3.0/

Heat resistor for
Sensor Temperature controller
Generic values listed, to fix via test

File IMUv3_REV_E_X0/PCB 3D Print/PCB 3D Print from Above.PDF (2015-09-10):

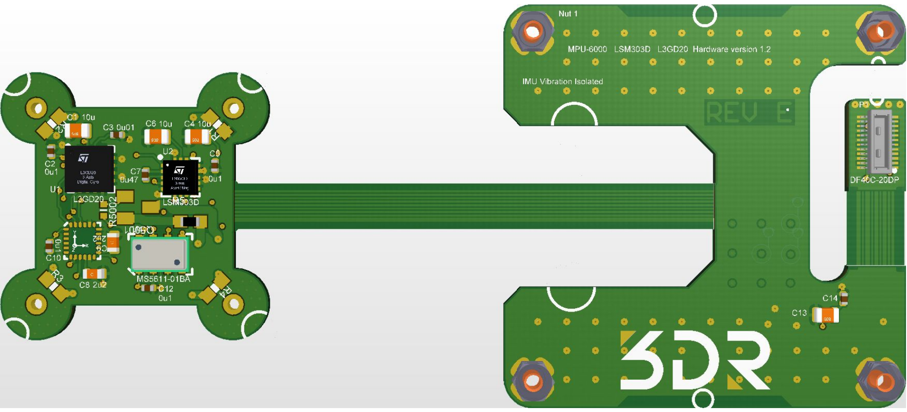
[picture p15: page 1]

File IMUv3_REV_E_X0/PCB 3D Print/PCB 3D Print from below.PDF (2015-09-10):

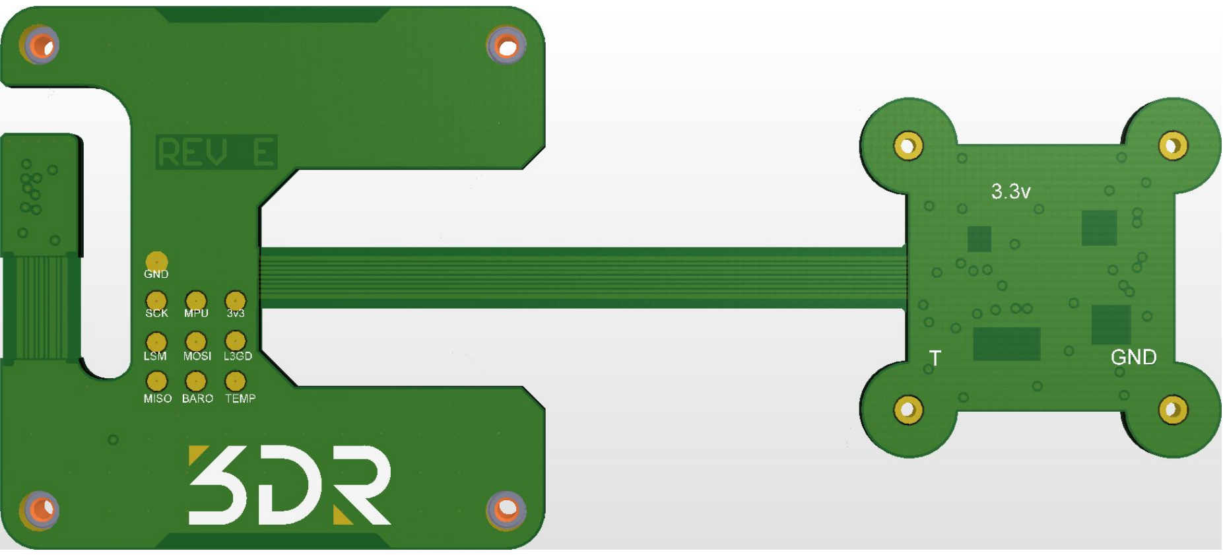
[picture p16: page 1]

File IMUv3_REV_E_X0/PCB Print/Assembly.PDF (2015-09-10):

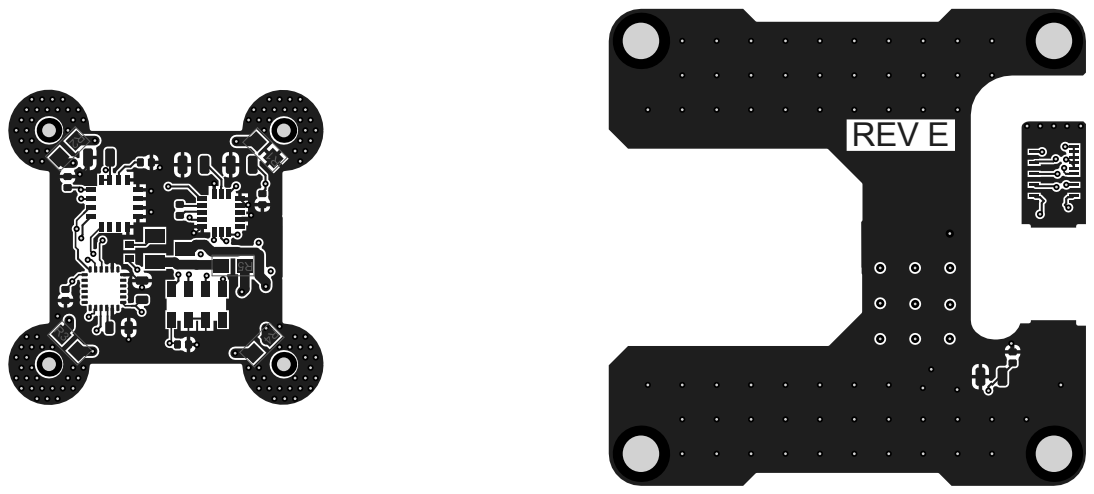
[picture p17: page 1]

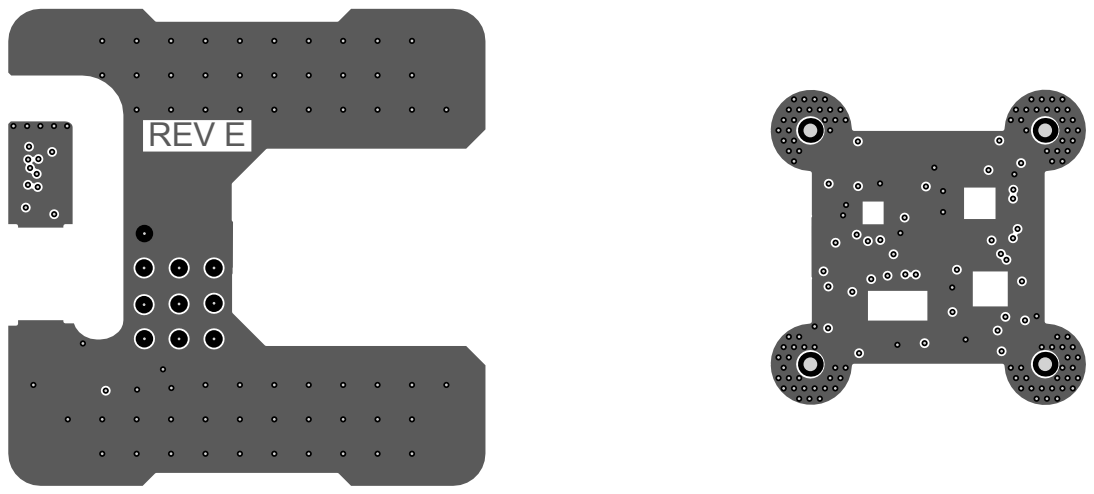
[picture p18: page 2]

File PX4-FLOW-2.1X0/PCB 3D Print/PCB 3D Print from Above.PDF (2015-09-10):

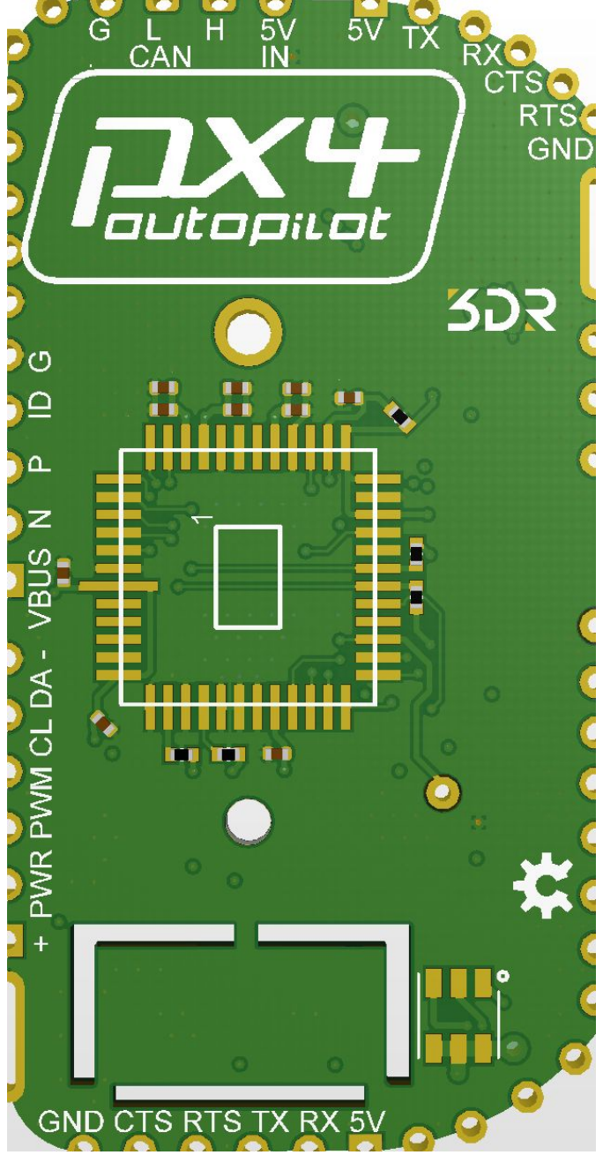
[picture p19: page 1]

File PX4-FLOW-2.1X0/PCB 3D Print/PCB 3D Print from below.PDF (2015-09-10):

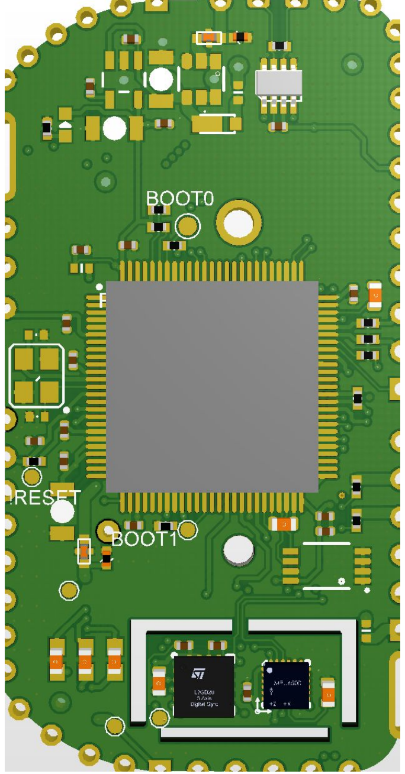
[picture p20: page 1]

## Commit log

2015-06-04 initial commit
    Rev_D OSHW Pixhawk 2 files
    [80PIN_FMU3_REV_C.SchDoc, Bill of Materials-FMU3_REV_D(FMU3_REV_D).xlsx, Bill of Materials-PSM_REV_C(PCA_0007_PSM).xlsx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]
2015-06-23 Added Pick and place notes for FMU
    [2.0_X0.PcbDoc, FMU3_REV_D.PrjPcb, IMU_REV_C.PrjPcb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]
2015-07-10 update to IMU_REV_D (Change thickness)
    Create Solo Accessory breakout
    [Accessory_Breakout_X1.GBL, Accessory_Breakout_X1.GBO, Accessory_Breakout_X1.GBP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]
2015-07-12 Flow, breakout, and IMU changes (IMU added silk to show flex locations)
    [Accessory_Breakout_X1.PcbDoc, Accessory_Breakout_X1.PrjPcb, IMU_REV_D.DXF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]
2015-07-13 First draft of Rev 2.0X Flow
    [PX4FLOW2.0_CPU_X0.SchDoc, PX4FLOW2.0_X0.PcbDoc, PX4FLOW2.0_X0.PrjPcb]
2015-07-13 cleaned up schematics
    [Bill of Materials-PX4FLOW2.0_X0(PX4FLOW2.xls, PX4FLOW2.0_CAM_X0.SchDoc, PX4FLOW2.0_CPU_X0.SchDoc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]
2015-07-22 Flow 2.0 version x0
    [Bill of Materials-PX4FLOW2.0_X0(PX4FLOW2.xls, PX4FLOW2.0_CPU_X0.SchDoc, PX4FLOW2.0_Connectors_X0.SchDoc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]
2015-07-23 Optical Flow
    Mods to remove wires from unconnected pins on processor.
    Connected two spare pins to Connector 10
    Labeled all pins on the back of the PCB
    [IMU_REV_D.PcbDoc, PX4FLOW2.0_CPU_X0.SchDoc, PX4FLOW2.0_Connectors_X0.SchDoc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]
2015-07-28 Factory files, and thickness change for IMU (1.15mm to 1.1mm)
    [1510510464.sldasm, 473460001.sldasm, 5023820470.sldasm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]
2015-07-31 REV_E FMU first pass Changed the level shifter to a high current (10ma)shifter for the FMU I/O Added the ability to choose 5v or 3.3v servo outs for 1-8 by cutting a track, and solder jumping a pad..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
    [80PIN_FMU3_REV_C.SchDoc, 80PIN_FMU3_REV_E.SchDoc, CHANGE_FMU3_REV_D.SchDoc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]
2015-09-01 IMU and FMU latest Flow 2.1
    [Bill of Materials-IMU_REV_D_1(IMU_REV_D).xls, Bill of Materials-IMU_REV_E(IMU_REV_E).xls, Bill of Materials-IMU_REV_F(IMU_REV_F).xls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]
2015-09-08 FMU_G and IMU_E
    [80PIN_FMU3_REV_G.SchDoc, CHANGE_FMU3_REV_G.SchDoc, FMU3_REV_G.PrjPcb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]
2015-09-10 Mainly Flow changes
    [Bill of Materials-FMU3_REV_G(FMU3_REV_G).xls, Bill of Materials-IMU_REV_E(IMU_REV_E).xls, Bill of Materials-PCA_0005_FULL_CB_REV_B.xls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]
2015-10-28 update outputs on PH2 carrier boards
    [Bill of Materials-PCA_0005_FULL_CB_REV_B(PCA_0012_INTEL_CB).xls, Bill of Materials-PCA_0006_Mini_CB_REV_B(PCA_0006_Mini_CB).xls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]
